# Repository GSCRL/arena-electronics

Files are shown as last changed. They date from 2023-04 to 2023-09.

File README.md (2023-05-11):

# arena-electronics

# Other Repos

UI / Webserver - https://github.com/fubarlabs/RobotCombatOverlay
ESP32 Firmware - https://github.com/GSCRL/bot-arena-control
## Build Arg Notes

```ini
check_skip_packages = yes
lib_deps = bblanchon/ArduinoJson
build_flags = -O2 -D DEBUG_ESP_PORT=Serial
build_unflags = -Os
```

# Broker Setup

```
allow_anonymous true

listener 1883
protocol mqtt

listener 9001
protocol websockets
```

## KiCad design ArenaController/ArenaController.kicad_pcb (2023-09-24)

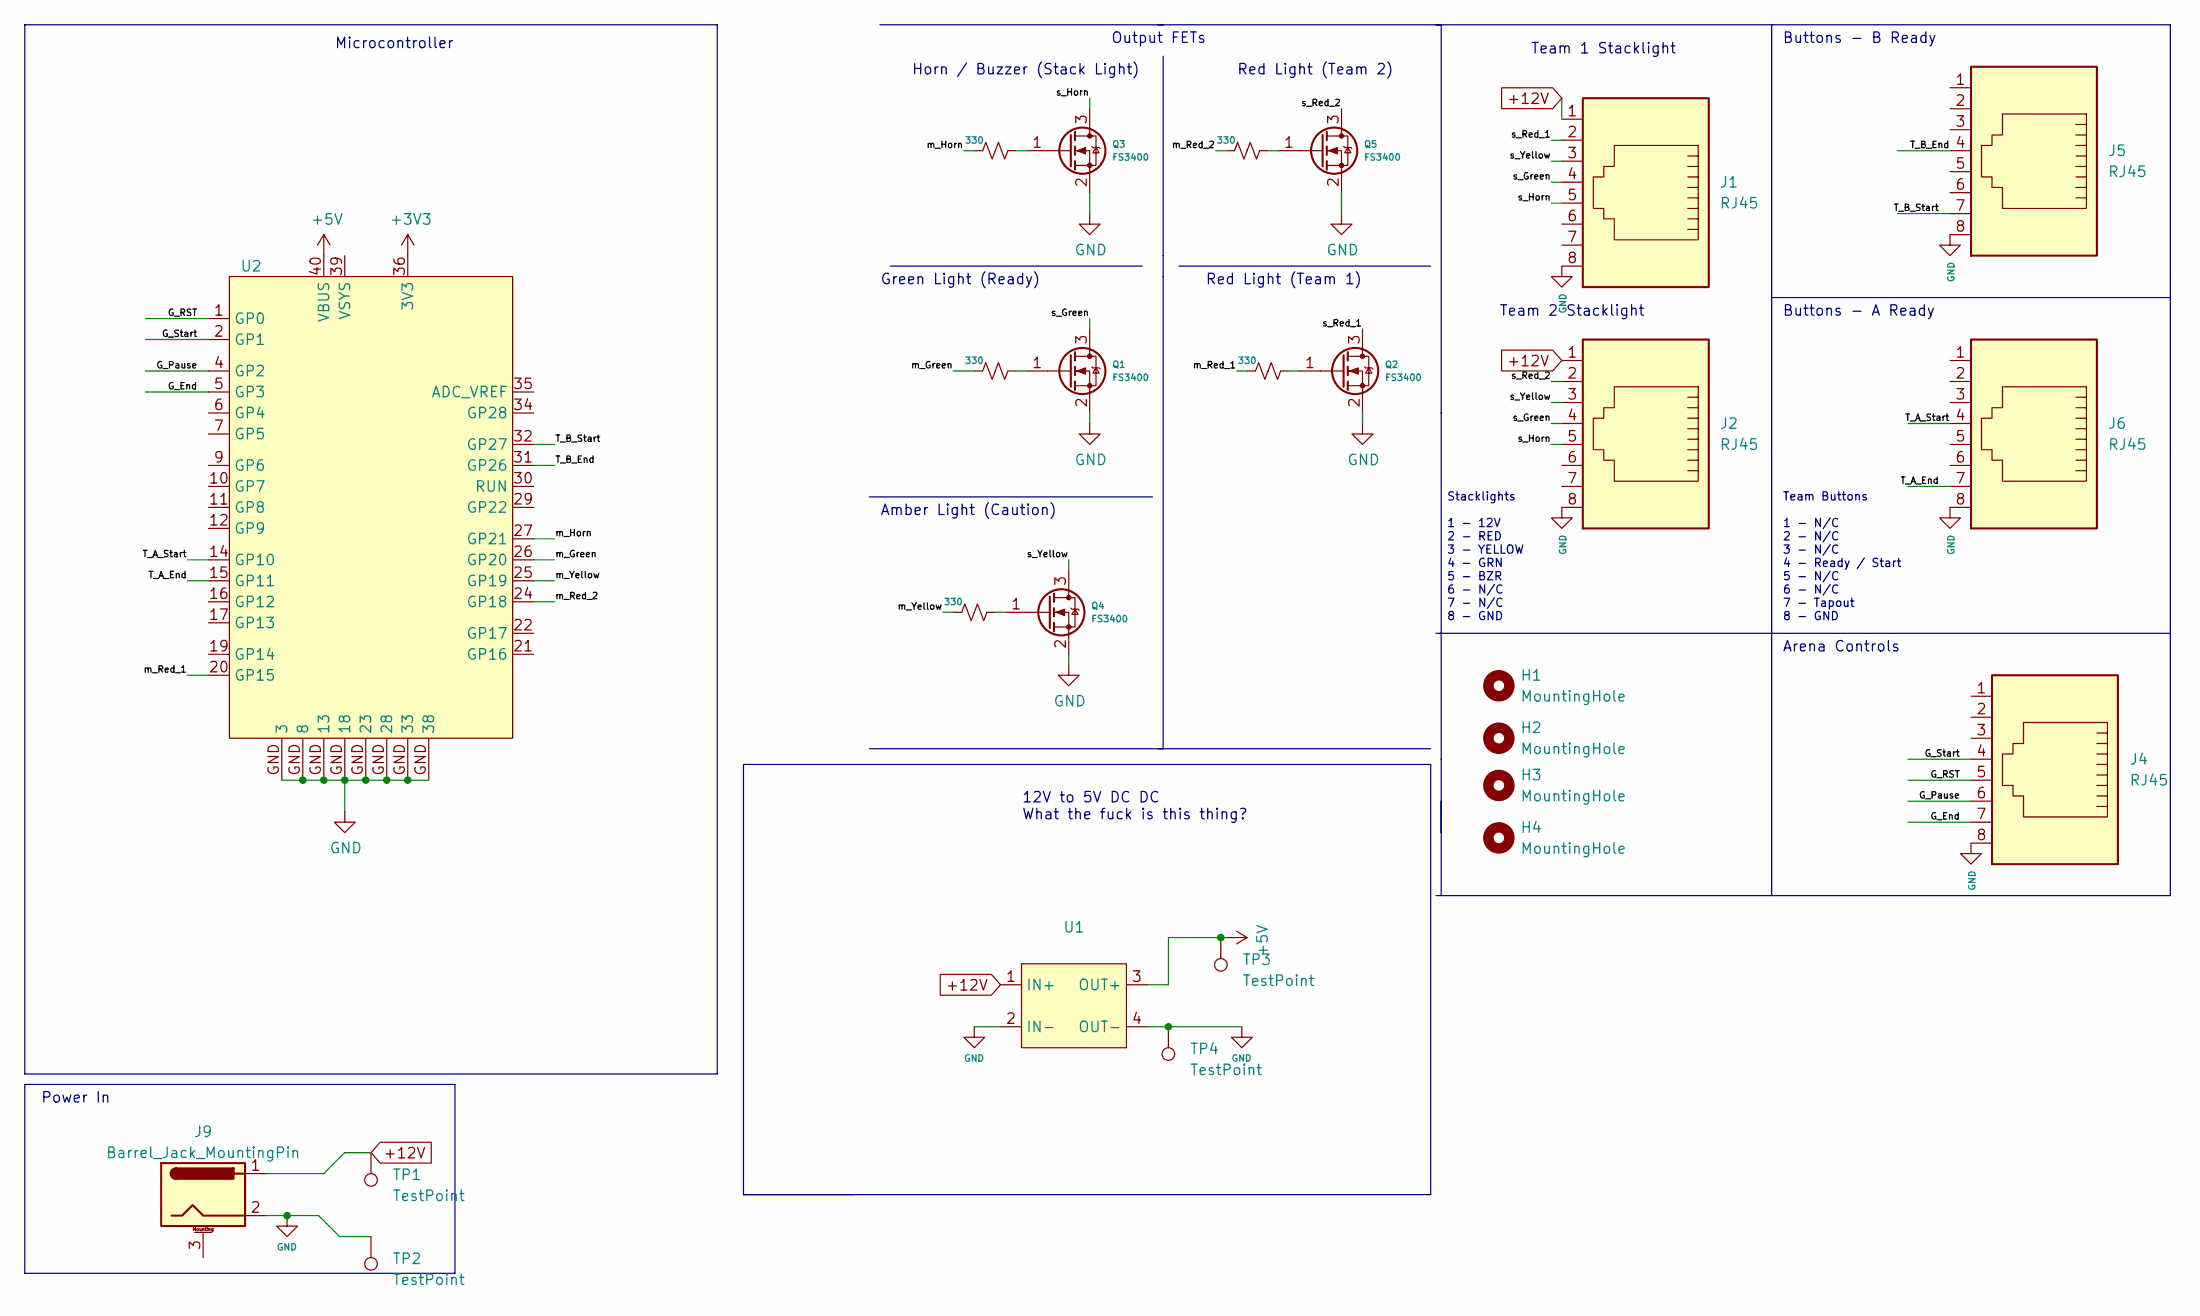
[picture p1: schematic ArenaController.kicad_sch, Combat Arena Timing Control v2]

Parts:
H1, H2, H3, H4: MountingHole; MountingHole_3.2mm_M3
J1, J2, J4, J5, J6: RJ45; RCH RC00139
J9: Barrel_Jack_MountingPin; BarrelJack_Horizontal
Q1, Q2, Q3, Q4, Q5: FS3400; SOT-23
R1, R2, R3, R4, R5: 330; R_1206_3216Metric_Pad1.30x1.75mm_HandSolder
TP1, TP2, TP3, TP4: TestPoint; TestPoint_Loop_D1.80mm_Drill1.0mm_Beaded
U1: LM2596_Module
U2: Raspberry_Pi_Pico_SMT_THT

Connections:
+3V3: U2.36 (3V3)
+5V: TP3.1, U1.3 (OUT+), U2.40 (VBUS)
+12V: J1.1, J2.1, J9.1, TP1.1, U1.1 (IN+)
/G_End: J4.7, U2.5 (GP3)
/G_Pause: J4.6, U2.4 (GP2)
/G_RST: J4.5, U2.1 (GP0)
/G_Start: J4.4, U2.2 (GP1)
/T_A_End: J6.7, U2.15 (GP11)
/T_A_Start: J6.4, U2.14 (GP10)
/T_B_End: J5.4, U2.31 (GP26)
/T_B_Start: J5.7, U2.32 (GP27)
/m_Green: R1.2, U2.26 (GP20)
/m_Horn: R2.2, U2.27 (GP21)
/m_Red_1: R5.2, U2.20 (GP15)
/m_Red_2: R4.2, U2.24 (GP18)
/m_Yellow: R3.2, U2.25 (GP19)
/s_Green: J1.4, J2.4, Q1.3 (D)
/s_Horn: J1.5, J2.5, Q3.3 (D)
/s_Red_1: J1.2, Q2.3 (D)
/s_Red_2: J2.2, Q5.3 (D)
/s_Yellow: J1.3, J2.3, Q4.3 (D)
GND: J1.8, J2.8, J4.8, J5.8, J6.8, J9.2, Q1.2 (S), Q2.2 (S), Q3.2 (S), Q4.2 (S), Q5.2 (S), TP2.1, TP4.1, U1.2 (IN-), U1.4 (OUT-), U2.GND (13)
unnamed: Q1.1 (G), R1.1
unnamed: Q2.1 (G), R5.1
unnamed: Q3.1 (G), R2.1
unnamed: Q4.1 (G), R3.1
unnamed: Q5.1 (G), R4.1

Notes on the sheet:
Amber Light (Caution)
Arena Controls
Microcontroller
Green Light (Ready)
Buttons - A Ready
Team 2 Stacklight
12V to 5V DC DC What the fuck is this thing?
Power In
Team 1 Stacklight
Output FETs
Horn / Buzzer (Stack Light)
Team Buttons 1 - N/C 2 - N/C 3 - N/C 4 - Ready / Start 5 - N/C 6 - N/C 7 - Tapout 8 - GND
Buttons - B Ready
Red Light (Team 1)
Red Light (Team 2)
Stacklights 1 - 12V 2 - RED 3 - YELLOW 4 - GRN 5 - BZR 6 - N/C 7 - N/C 8 - GND

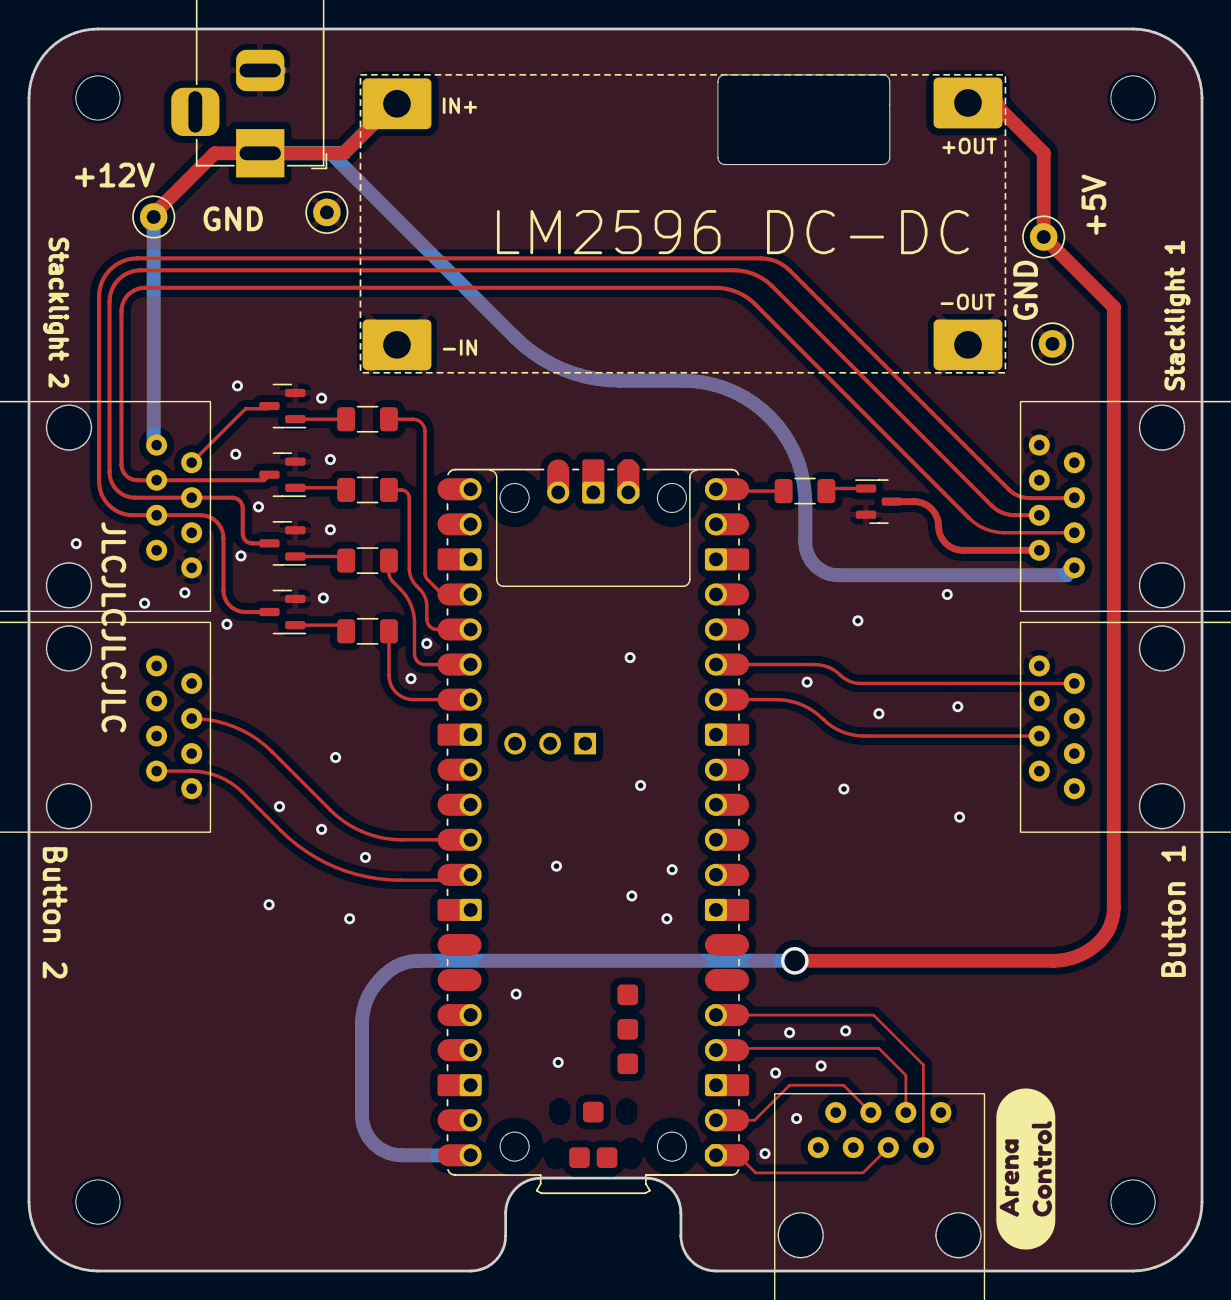
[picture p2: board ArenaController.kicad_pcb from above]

Board: 2 copper layers, 85.0 x 90.0 mm, 27 parts (0 on the bottom side), 26 nets.

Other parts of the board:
kibuzzard-638A219C: G***; kibuzzard-638A219C

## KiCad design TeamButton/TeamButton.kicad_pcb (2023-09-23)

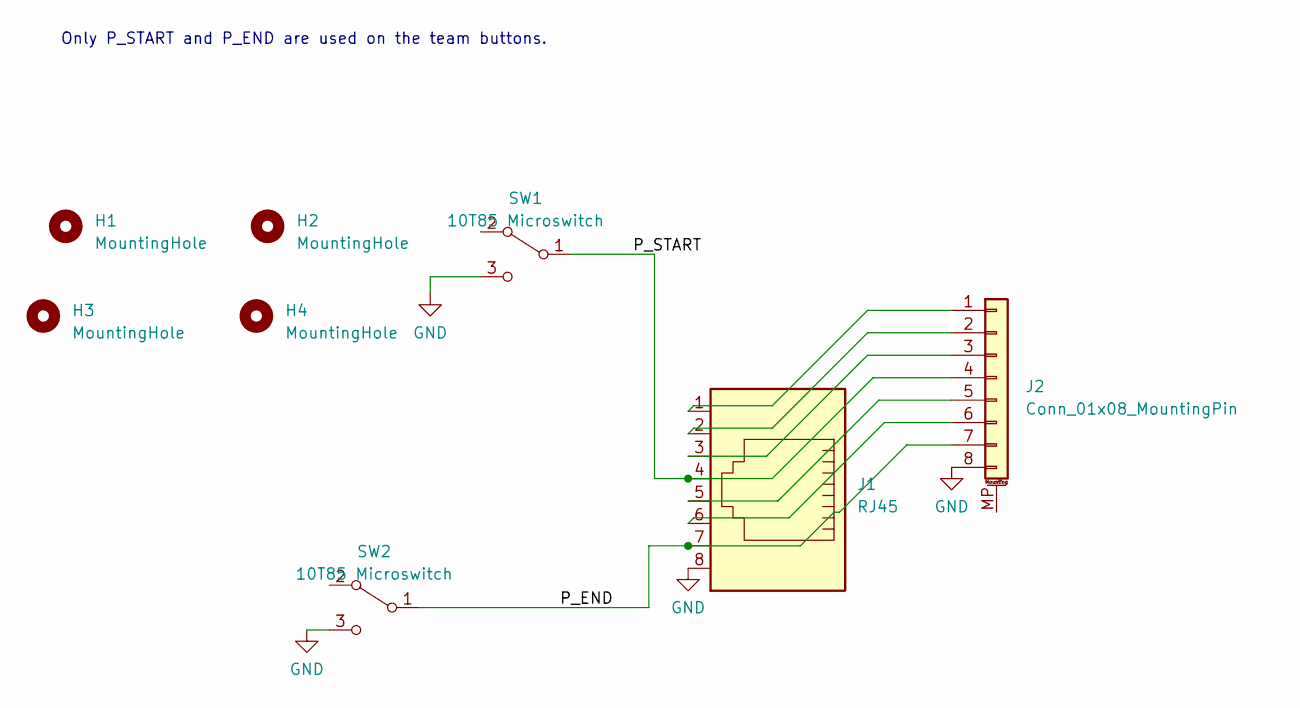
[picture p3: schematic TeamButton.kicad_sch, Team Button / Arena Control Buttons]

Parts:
H1, H2, H3, H4: MountingHole; MountingHole_3.2mm_M3
J1: RJ45; RCH RC00139
J2: Conn_01x08_MountingPin; PinSocket_1x08_P2.54mm_Horizontal
SW1, SW2: 10T85 Microswitch; 10T85 Microswitch with M3 mounts

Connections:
/P_END: J1.7, J2.7, SW2.1 (C)
/P_START: J1.4, J2.4, SW1.1 (C)
GND: J1.8, J2.8, SW1.3 (NO), SW2.3 (NO)
unnamed: J1.1, J2.1
unnamed: J1.2, J2.2
unnamed: J1.3, J2.3
unnamed: J1.5, J2.5
unnamed: J1.6, J2.6

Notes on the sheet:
Only P_START and P_END are used on the team buttons.

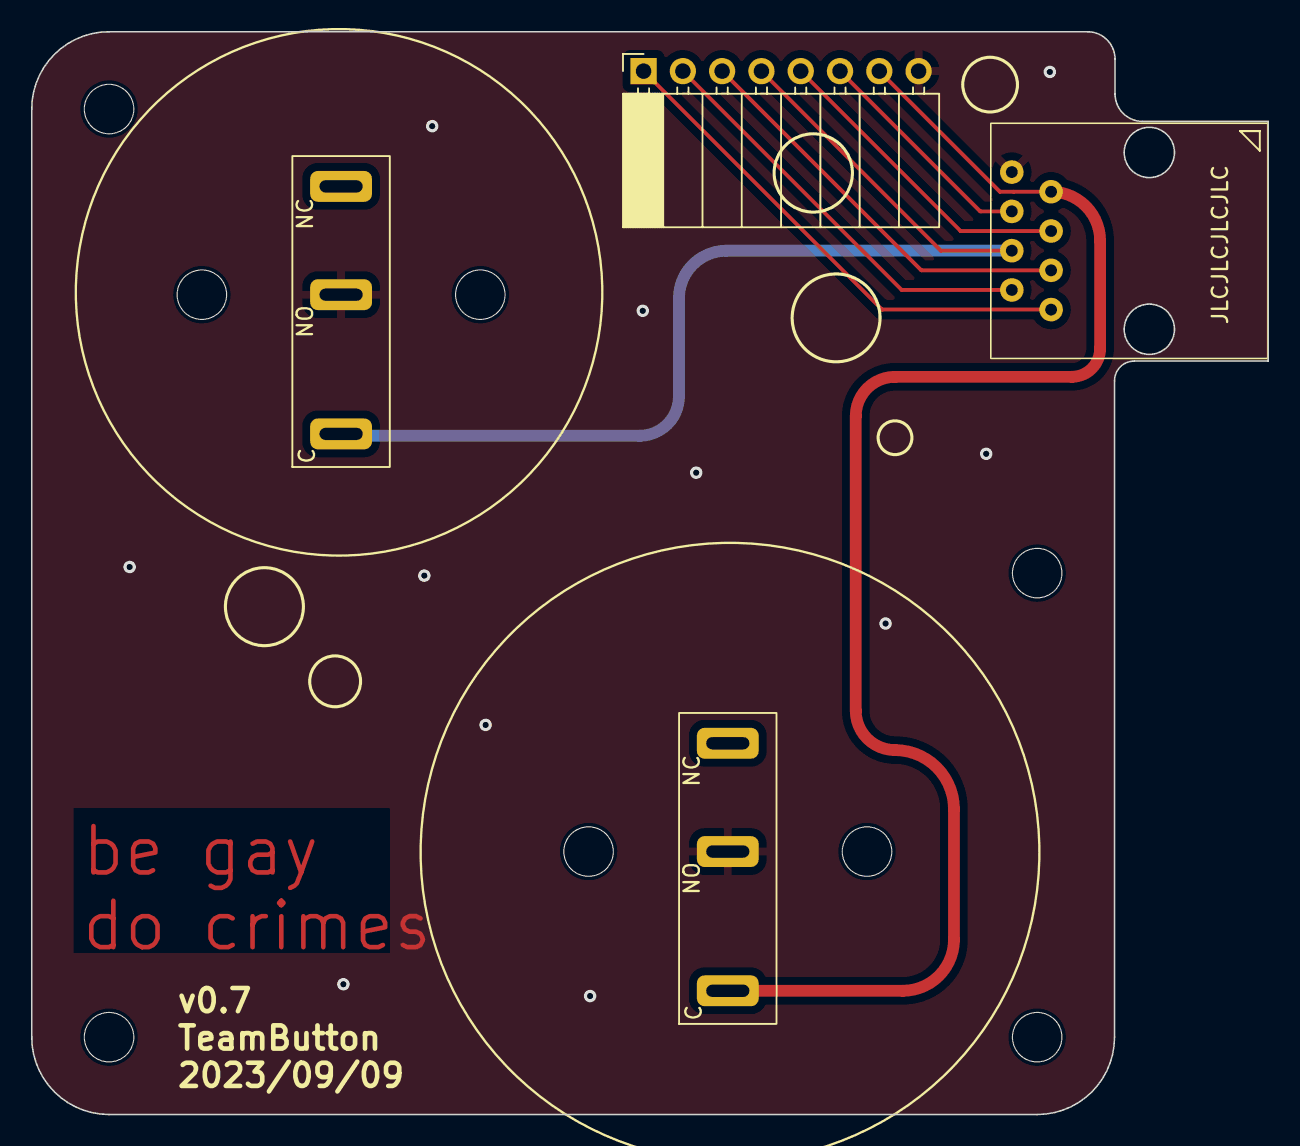
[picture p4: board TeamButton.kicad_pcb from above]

Board: 2 copper layers, 79.9 x 70.0 mm, 8 parts (0 on the bottom side), 8 nets.

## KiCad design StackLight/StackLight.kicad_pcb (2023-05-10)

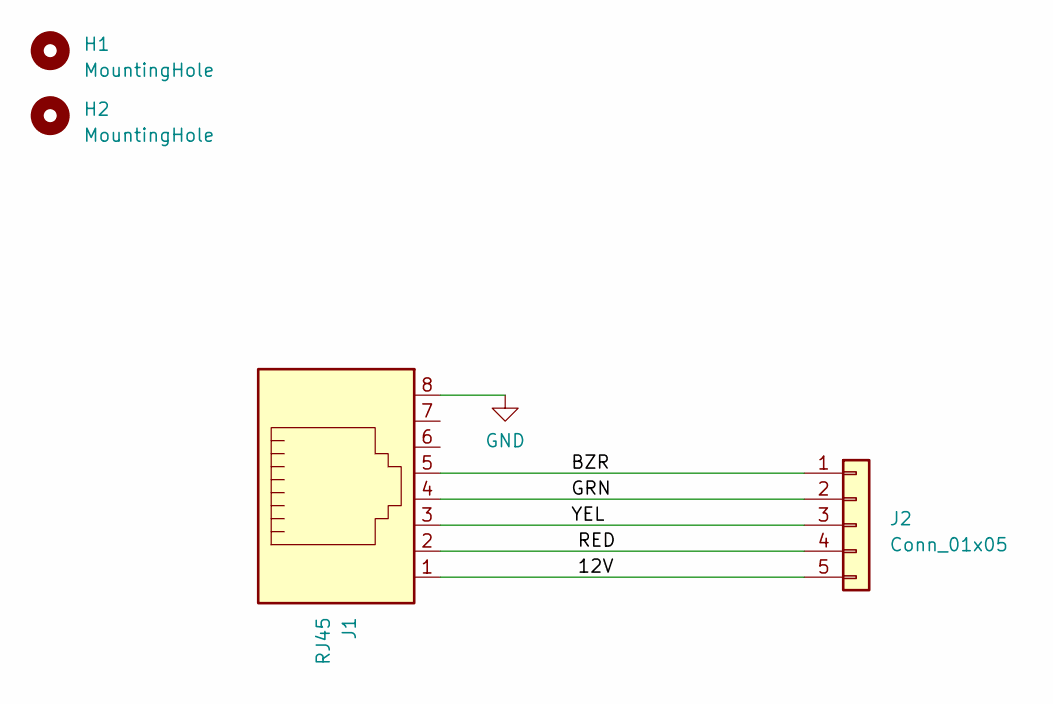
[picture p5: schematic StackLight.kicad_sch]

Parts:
H1, H2: MountingHole; MountingHole_3.2mm_M3
J1: RJ45; RCH RC00139
J2: Conn_01x05; SolderWire-1.5sqmm_1x05_P6mm_D1.7mm_OD3mm_Relief

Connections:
/12V: J1.1, J2.5
/BZR: J1.5, J2.1
/GRN: J1.4, J2.2
/RED: J1.2, J2.4
/YEL: J1.3, J2.3
GND: J1.8

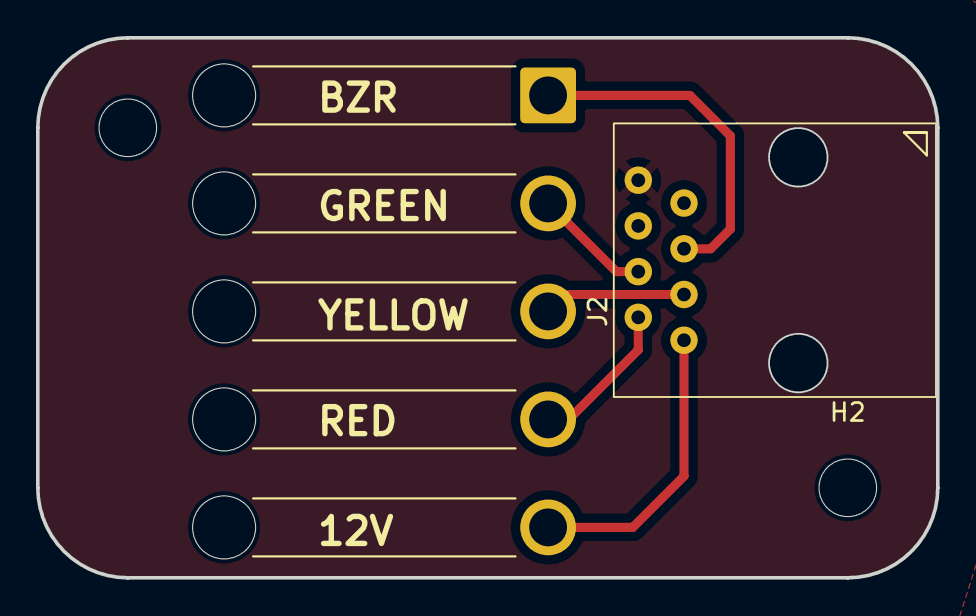
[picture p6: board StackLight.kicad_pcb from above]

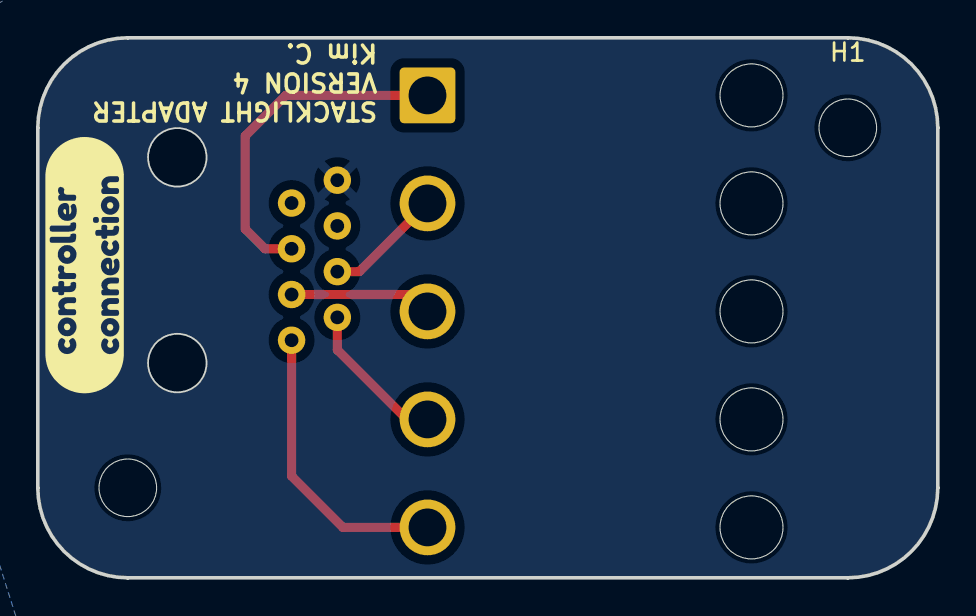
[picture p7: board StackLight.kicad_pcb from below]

Board: 2 copper layers, 50.0 x 30.0 mm, 5 parts (2 on the bottom side), 5 nets.

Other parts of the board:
kibuzzard-631545B4: G***; kibuzzard-631545B4

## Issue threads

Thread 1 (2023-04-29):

GPIO0 Use / Unable To Use Correct Pins

MC42, 2023-04-29:
Cannot use these pins for ESP32 DevkitC v4:

https://randomnerdtutorials.com/esp32-pinout-reference-gpios/

MC42, 2023-04-29:
Resolved in #decb0dff3449769d9eb318a582d3a359adc5a449

Closed 2023-04-29.

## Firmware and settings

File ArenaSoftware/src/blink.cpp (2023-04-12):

#include <Arduino.h>
#include <PushButton.h>

/*
** Robot Combat Arena Control Code
** Using Ardunio framework / ESP32 (maybe STM32 with GPIO changes)
** Read 8 buttons
** ready and tap out for 2 teams
** Match start / pause / end /reset for ref
** Serial out to hacked iCruze display boards
** Will control 1 or 2 "stoplight" towers with signal horns
** NF 2022/06/04

*/

// State diagram
/* no match states:
    Reset and ready for start ( solid yellow )
      team a ready
      team b ready
      both teams ready (blinking yellow)
    match pause (blinking yellow or blinking red / match timer paused)
    match tapout (blinking red)
    match end by KO (blinking red)
    match end by time (solid red)
  Match states
    Start pressed (3 secs of blinking yellow followed by green.  Match timer starts then)
    start pressed after pause (same as above with timer resuming)
    active match (solid green)
    10 sec count down (blinking green)
  Horn will sound at match end, time up or team tapout
*/
// inline echo for debug
#define DEBUG_ON 1
#define DEBUG_OFF 0
byte debugMode = DEBUG_ON;

#define DBG(...) debugMode == DEBUG_ON ? Serial.println(__VA_ARGS__) : NULL
#define DEBUG

// button GPIO's ESP32 / Change for STM32
#define TEAM_A_START 23
#define TEAM_A_END 22
#define TEAM_B_START 33
#define TEAM_B_END 32
#define MATCH_START 25
#define MATCH_PAUSE 26
#define MATCH_END 27
#define MATCH_RESET 14
// tower signal light GPIO's
#define R_LIGHT 2
#define Y_LIGHT 4
#define G_LIGHT 5
#define HORN 13

#define D_SER_TX 17
#define D_SER_RX 16

#define MATCH_LEN 180 // match len in sec ( 3 min)
#define MATCH_END_WARN 15 // ending warn time sec
#define BLINK_DELAY 500 // in ms
#define STARTUP_DELAY 3000 //3 sec
#define MAIN_LOOP_DELAY 5 // in ms
#define HORN_SHORT 1000 //ms
#define HORN_LONG 2000 //ms
#define DIS_DELAY 200 //ms display update rate

PushButton Start_A(TEAM_A_START);
PushButton End_A(TEAM_A_END);
PushButton Start_B(TEAM_B_START);
PushButton End_B(TEAM_B_END);
PushButton GameStart(MATCH_START);
PushButton GameOver(MATCH_END);
PushButton GamePause(MATCH_PAUSE);
PushButton GameReset(MATCH_RESET);

uint64_t Btn_timer;
uint64_t light_timer;
uint64_t Horn_timer;
uint64_t Timer_timer;
uint64_t Display_timer;
uint64_t Dis_min;
uint64_t Dis_sec;

// Match state
enum MatchState{ all_ready, team_a_ready, team_b_ready, starting, in_progress, ending, unpaused, paused, team_a_tap, team_b_tap, time_up, ko_end };
enum MatchState g_match;
bool g_Match_Reset;

uint64_t gMatchRunTime; //match run time ms
uint64_t gMatchStartTime; //match start time ms
uint64_t MatchSecRemain; // sec remaining
int64_t CountDownMSec; // count down
uint8_t isTimerRunning;
uint64_t gSDtimer; // used for start delay
uint64_t gBLtimer; // for light blinking
uint8_t gBLstate; // for light blinking
uint64_t gTootTimer; //for horn
uint8_t gHornState; // for horn
uint8_t gHornBlast;

// button reading and state setting is done here
void readBtns(MatchState &match, bool &Match_Reset)
{
  // note the button.cycleCount() resets the button press counter
  uint8_t BtnCycle;

  // if match is running these buttons are active
    if (match == MatchState::in_progress)
    {
      End_A.update();
      End_B.update();
      GameOver.update();
      GamePause.update();
      Match_Reset = false;
      DBG("test IP");
      // pause hit
      if (GamePause.isCycled())
      {
        BtnCycle = GamePause.cycleCount();
        match = MatchState::paused;
      }
      // team tap out
      if ((End_A.isCycled() || End_B.isCycled()) && (match == MatchState::in_progress))
      {
        // Team A has tapped out
        if(End_A.isCycled())
          match = MatchState::team_a_tap;
        // Team B has tapped out
        if(End_B.isCycled())
          match = MatchState::team_b_tap;
        BtnCycle = End_A.cycleCount();
        BtnCycle = End_B.cycleCount();
      }

      // Ref has ended the match
      if(GameOver.isCycled() && (match == MatchState::in_progress)) 
      {
        BtnCycle = GameOver.cycleCount();
        match = MatchState::ko_end;
      }
    }
    else
    // match is ended these are active
    // starting is the match start countdown state
    if ((match != MatchState::starting)||(match != MatchState::paused)||(match != MatchState::unpaused))
    {
      {
        GameStart.update();
        Start_A.update();
        Start_B.update();
        GameReset.update();
        //DBG("test Start");
        // this discards the reads on A, B and main start if not reset
        if (Match_Reset == false)
        {
          BtnCycle = Start_A.cycleCount();
          BtnCycle = Start_B.cycleCount();
          BtnCycle = GameStart.cycleCount();
        }
        if (GameReset.isCycled())
        {
          Match_Reset = true;
          BtnCycle =GameReset.cycleCount();
        }

        // check to see if both teams are ready
        if (Start_A.isCycled() and Start_B.isCycled())
        {
          match = MatchState::all_ready;
          BtnCycle = Start_A.cycleCount();
          BtnCycle = Start_B.cycleCount();
        }
        else
        {
          if (Start_A.isCycled())
          {
            match = MatchState::team_a_ready;
          }
          if (Start_B.isCycled())
          {
            match = MatchState::team_b_ready;
          }
        }
        // if everyone is ready and start is pressed
        if (GameStart.isCycled() and (match == MatchState::all_ready))
        {
          BtnCycle = GameStart.cycleCount();
          BtnCycle = GameReset.cycleCount();
          match = MatchState::starting;
        }
      }
    }
    // match paused
    else
    {
      if(match == MatchState::paused)
      {
        GameStart.update();
        if(GameStart.isCycled())
        {
          match = unpaused;
          BtnCycle = GameStart.cycleCount();
        }
      }
    }

}

// used to blink the light tower
void blink(u_int8_t &state, uint64_t &lastBlink, u_int8_t ledGPIO)
{
  if((millis() - lastBlink) > BLINK_DELAY)
  {
    if (state > 0)
    {
      digitalWrite(ledGPIO, HIGH);
      state = 0;
    }
    else
    {
      digitalWrite(ledGPIO, LOW);
      state = 1;
    }
    lastBlink = millis();
  }
}

// handle lights here
void setLights(MatchState &match, u_int8_t Match_Reset, u_int64_t &SDtimer)
{
  
// all lights off
  if((Match_Reset) && (match != MatchState::starting))
  {
    digitalWrite(G_LIGHT,LOW);
    digitalWrite(Y_LIGHT,LOW);
    digitalWrite(R_LIGHT,LOW);
  }
  // match in progress
  if (match == in_progress)
  {
    digitalWrite(G_LIGHT,HIGH);
    digitalWrite(Y_LIGHT,LOW);
    digitalWrite(R_LIGHT,LOW);
  }
  // match is stopped
  // if ((g_match != in_progress) || (g_match != starting) || (g_match != paused) || (g_match != unpaused))
  // not sure if enum can be used this way
  if ((match < 3) && (match > 6))
  {
    digitalWrite(G_LIGHT,LOW);
    //digitalWrite(Y_LIGHT,LOW);
    digitalWrite(R_LIGHT,HIGH);
  }
  // match is starting
  // blink yellow for 3 sec, red out, green out
  if(match == MatchState::starting)
  {
    if((millis()-SDtimer) < STARTUP_DELAY)
      blink(gBLstate, gBLtimer, Y_LIGHT);
    else
      match=MatchState::in_progress;
    SDtimer = millis();
  }
  // match is paused
  // red is lit yellow is blinking
  if(match == MatchState::paused)
  {
    blink(gBLstate, gBLtimer, Y_LIGHT);
    digitalWrite(R_LIGHT,HIGH);
  }
  // match is ending (within 15 sec of end)
  // blink green
  if(match == MatchState::ending)
  {
    blink(gBLstate, gBLtimer, G_LIGHT);
  }

  // to do when everything working
  // Team A tap blink A tower red
  // Team B tap blink B tower red
  // for now just blink both towers red
}

// light debug function
void LightDebugPrint(MatchState &match, u_int8_t Match_Reset, u_int64_t &SDtimer)
{
  switch (match)
  {
  case MatchState::all_ready:
    Serial.println("All ready");
    break;
  case MatchState::team_a_ready:
    Serial.println("team_a_ready");
    break;
  case MatchState::team_b_ready:
    Serial.println("team_b_ready");
    break;
  case MatchState::starting:
    Serial.println("starting");
    break;
  case MatchState::in_progress:
    Serial.println("in_progress");
    break;
  case MatchState::ending:
    Serial.println("ending");
    break;
  case MatchState::unpaused:
    Serial.println("unpaused");
    break;
  case MatchState::paused:
    Serial.println("paused");
    break;
  case MatchState::team_a_tap:
    Serial.println("team_a_tap");
    break;
  case MatchState::team_b_tap:
    Serial.println("team_b_tap");
    break;
  /*case MatchState::time_up:
    Serial.println("time_up");
    break;
  case MatchState::ko_end:
    Serial.println("ko_end");*/
  default:
    break;
  }
  if(match == MatchState::starting)
  {
    if((millis()-SDtimer) < STARTUP_DELAY)
      blink(gBLstate, gBLtimer, Y_LIGHT);
    else
      match=MatchState::in_progress;
    SDtimer = millis();
  }
}

// used to sound horn (yet another timer)
void soundHorn(u_int8_t &hornBlast, uint64_t &hornTime, u_int32_t tootLen, u_int8_t GPIO)
{
  u_int8_t state  = hornBlast % 2;
  if((millis() - hornTime) > tootLen)
  {
    if (state > 0)
    {
      digitalWrite(GPIO, HIGH);
    }
    else
    {
      digitalWrite(GPIO, LOW);
    }
    hornTime = millis();
    hornBlast++;
  }
}
// update and display match time
void match_timer(u_int64_t StartTime, u_int64_t &timerValue, u_int8_t &running)
{
  if ((running) && (timerValue < MATCH_LEN * 1000))
    timerValue = millis() - StartTime;
  else
    running = false;
}

void setup() {
  Serial.begin(115200);
  Serial1.begin(9600,SERIAL_8N1,D_SER_RX,D_SER_TX);
  pinMode(R_LIGHT,OUTPUT);
  pinMode (Y_LIGHT,OUTPUT);
  pinMode (G_LIGHT, OUTPUT);
  // check lights
  digitalWrite(G_LIGHT,HIGH);
  digitalWrite(Y_LIGHT,HIGH);
  digitalWrite(R_LIGHT,HIGH);
  Serial.println("test");
  delay(1000);
  digitalWrite(G_LIGHT,LOW);
  digitalWrite(Y_LIGHT,LOW);
  digitalWrite(R_LIGHT,LOW);
  // check horn
  digitalWrite(HORN,HIGH);
  delay(200);
  digitalWrite(HORN,LOW);
  g_Match_Reset = false;
  isTimerRunning = false;
  gMatchRunTime = 0;
  gMatchStartTime = 0;
  gSDtimer = 0;
  CountDownMSec = 0;
  gBLtimer = millis();
  Btn_timer = millis();
  g_match = MatchState::time_up;
  Serial1.println("---Display Test----");
  Serial1.println("---Line 2----");
}

void loop() 
{
  
  // Button reading is here
  if ((millis()-Btn_timer) > MAIN_LOOP_DELAY)
  {
    readBtns(g_match, g_Match_Reset);
    DEBUG("test prime");
    // set startup delay - match will be inprogress after this is done
    if ((g_match == MatchState::starting)&&(gSDtimer == 0))
      gSDtimer = millis();
    else if (g_match == MatchState::starting)
    {
      CountDownMSec = STARTUP_DELAY -(millis() - gSDtimer);
      if (CountDownMSec < 5)
      {
        // start match reset count down timer
        g_match = MatchState::in_progress;
        CountDownMSec = 0;
        gSDtimer = 0;
      }
    }
    Btn_timer = millis();
  }
  // handle lights
  #ifdef DEBUG
  if ((millis()-light_timer) > MAIN_LOOP_DELAY + 200)
  {
    LightDebugPrint(g_match, g_Match_Reset, gSDtimer);
    light_timer = millis();
  }
  #else
  if ((millis()-light_timer) > MAIN_LOOP_DELAY + 1)
  {
    setLights(g_match, g_Match_Reset, gSDtimer);
    light_timer = millis();
  }
  #endif
  // handle horn
  #ifdef DEBUG
  #else
  if ((millis()- Horn_timer) > MAIN_LOOP_DELAY * 2 )
  {
      // short horn on start or pause
      /*
      if(g_match == MatchState::starting)
      {
        while (gHornBlast < 6)
        {
          soundHorn(gHornBlast,gTootTimer,HORN_SHORT,HORN);
        }
      }
      else
        if(g_match < 8)
          gHornBlast = 0;
      // long horn on match end
      if(g_match > 7)
      {
        while (gHornBlast < 2)
        {
          soundHorn(gHornBlast,gTootTimer,HORN_LONG,HORN);
        }
      }
      else
        if(g_match!=MatchState::starting)
          gHornBlast = 0;
      */
      Horn_timer = millis();
  }
  #endif

  // update match timer
  if ((millis() + Timer_timer) > MAIN_LOOP_DELAY)
  {
    //start timer
    if((g_match == MatchState::in_progress)&&(isTimerRunning == false))
    {
      gMatchStartTime = millis();
      isTimerRunning = true;
    }
    //restart after pause
    if((g_match == MatchState::unpaused)&&(isTimerRunning == false))
    {
      isTimerRunning = true;
      g_match = MatchState::in_progress;
    }
    //stop timer
    if(g_match != MatchState::in_progress)
      isTimerRunning = false;

    //update timer
    if(((g_match == MatchState::in_progress)||(g_match == MatchState::ending))&&(isTimerRunning == true))
    {
      match_timer(gMatchStartTime, gMatchRunTime, isTimerRunning);
      if(isTimerRunning == false)
        g_match = MatchState::time_up;
    }
    // check for match ending
    MatchSecRemain = MATCH_LEN - ((gMatchRunTime - gMatchStartTime)/1000);
    if (MatchSecRemain < MATCH_END_WARN)
      g_match  = MatchState::ending;
    Timer_timer = millis();
  }

  // update char display
  // will send info out via serial
  if ((millis()-Display_timer) > DIS_DELAY)
  {
    // using the 2 x 20 line iCruze display
    // refresh display every 200 ms 
    // display time remaining in min : sec on first line
    // status display on second
    Dis_min = MatchSecRemain / 60;
    Dis_sec = MatchSecRemain % 60;
    if(g_match == MatchState::in_progress)
    {
      Serial1.print(Dis_min);
      Serial1.print(":");
      Serial1.printf("%02d",Dis_sec);
      Serial1.println(" Remaining");
      Serial1.println("Match in Progress");
    }
    if(g_match == MatchState::paused)
    {
      Serial1.print(Dis_min);
      Serial1.print(":");
      Serial1.printf("%02d",Dis_sec);
      Serial1.println(" Remaining");
      Serial1.println("--Paused --");
    }
    if(g_match == MatchState::starting)
    {
      Serial1.print("Starting in: ");
      Serial1.printf("%02d",(gSDtimer/1000));
      Serial1.println();
      Serial1.println("ALL READY-Starting");
    }
    if(g_match == MatchState::time_up)
    {
      Serial1.println("--- Time's Up ---");
      Serial1.println("-- MATCH OVER ---");
    }
    if(g_match == MatchState::team_a_tap)
    {
      Serial1.print(Dis_min);
      Serial1.print(":");
      Serial1.printf("%02d",Dis_sec);
      Serial1.println(" -MATCH OVER-");
      Serial1.println("--TEAM A TAPOUT--");
    }
    if(g_match == MatchState::team_b_tap)
    {
      Serial1.print(Dis_min);
      Serial1.print(":");
      Serial1.printf("%02d",Dis_sec);
      Serial1.println(" -MATCH OVER-");
      Serial1.println("--TEAM B TAPOUT--");
    }
    if(g_match == MatchState::ko_end)
    {
      Serial1.print(Dis_min);
      Serial1.print(":");
      Serial1.printf("%02d",Dis_sec);
      Serial1.println(" -MATCH OVER-");
      Serial1.println("-- BY KNOCKOUT --");
    }
    if(g_match == MatchState::all_ready)
    {
      Serial1.println("-- 3 min clock ---");
      Serial1.println("--- ALL READY ---");
    }
    if((g_match != MatchState::all_ready)&&(g_Match_Reset == true)&&(g_match != MatchState::starting))
    {
      Serial1.println("-- WAITING FOR ---");
      Serial1.println("----- READY -----");
    }
    Display_timer = millis();
  }
}

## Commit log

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2022-12-24 Add the funky stuff to start. This will be hell btw.
    [LightController.kicad_sch]
2022-12-24 Updated first half of schematic, mostlyish. Lots to go for lighting.
    [LightController.kicad_sch]
2022-12-25 Update roughly, using the same schematic for the 3v3 and 5v stuff, still need to figure out values, etc.
    [LightController.kicad_pcb, LightController.kicad_sch]
2022-12-30 Add footprints and shit.
    [LightController.kicad_pcb, LightController.kicad_sch]
2023-01-26 Bring in old schematic for cleanup / base work.
    [ArenaController.kicad_pcb, ArenaController.kicad_sch, ArenaController.sch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]
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2023-02-17 Add microswitch for start buttons.
    [ArenaController.kicad_pcb, ArenaController.kicad_sch]
2023-03-19 Added new files, swap to new FET for toggling, added FET as symbols.
    [ArenaController.kicad_pcb, ArenaController.kicad_sch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]
2023-03-22 Added new DC DC symbol.
    [ArenaController.kicad_pcb, ArenaController.kicad_sch]
2023-03-22 Added more SMD nightmare parts.
    [ArenaController.kicad_pcb, ArenaController.kicad_sch]
2023-03-22 Swapped to ESP32 Devkit 4.
    [ArenaController.kicad_pcb, ArenaController.kicad_sch]
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2023-03-27 small boardwork cleanup to try and lay it out.
    [ArenaController.kicad_pcb, ArenaController.kicad_sch]
2023-03-28 Started to organize board proper, did filled areas for 12V->5V input section.
    [ArenaController.kicad_pcb]
2023-03-29 Updated layout, added major routing. Still need connector for the WS2812B output and pin relayout.
    [ArenaController.kicad_pcb, ArenaController.kicad_sch]
2023-03-30 Tiny cleanup, workable version, yay.
    [ArenaController.kicad_pcb]
2023-03-31 Revision .4 layout with a sane ground plane, do fix the footprint shit tho
    [ArenaController.kicad_pcb, ArenaController.kicad_sch]
2023-04-05 Release v.4 for April event.
    [ArenaController-B_Cu.gbr, ArenaController-B_Mask.gbr, ArenaController-B_Paste.gbr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]
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2023-04-13 Updated team buttonboard to use M3 fasteners!
    [TeamButton.kicad_pcb, TeamButton.kicad_sch]
2023-04-14 Work day fixes for schematic, including re-polarizing the caps.
    [ArenaController.kicad_pcb, ArenaController.kicad_sch]
2023-04-14 Updated Button and Stacklight PCB to not have backwards fucking footprint shit.
    [StackLight.kicad_pcb, StackLight.kicad_sch, TeamButton.kicad_pcb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]
2023-04-14 Added SPIFFS note for if we need to use embedded FS stuff. Yay!
    [ArenaController.kicad_sch]
2023-04-14 Update to non-hole design. Verify wire gagues.
    [StackLight.kicad_pcb, StackLight.kicad_sch]
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2023-04-14 Added spacer mounting holes to board in case are needed. Insert through back first. Use smaller fasteners, etc. Only one hole should be needed.
    [TeamButton.kicad_pcb, TeamButton.kicad_sch]
2023-04-14 Added visual flourish and confirmed microswitch locations.
    [TeamButton.kicad_pcb]
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2023-04-14 Added wire strain relief that should fit.
    [StackLight.kicad_pcb, StackLight.kicad_sch]
2023-04-29 Update PCB errors and also remove software from this repo.
    [ArenaController-B_Cu.gbr, ArenaController-B_Mask.gbr, ArenaController-B_Paste.gbr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]
2023-04-29 Swap to a footprint with the correctly named pin in our project repo. Yay!
    [ArenaController.kicad_pcb, ArenaController.kicad_sch]
2023-05-04 Added initial teamsign and update symbol mistakes, mostly.
    [ArenaController.kicad_pcb, ArenaController.kicad_sch]
2023-05-04 Add team sign to gitignore and actually add stuff. Yay!
    [TeamSign.kicad_pcb, TeamSign.kicad_sch]
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2023-05-04 Update fp to include fixed keepouts for the THT part module.
    [ArenaController.kicad_pcb, ArenaController.kicad_sch]
2023-05-05 Initial footprint drag-in, add the svg, make the project libraries, and other stuff. Yay!
    [TeamSign.kicad_sch, three_digit.kicad_pcb]
2023-05-05 Add SK6812-Side-A footprint/symbol to working area, as well as swapped to a stacklight connection that has a ground pin at the end for generic 12v power use. yay!
    [ArenaController.kicad_pcb, ArenaController.kicad_sch, TeamSign.kicad_pcb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]
2023-05-06 Added subsheet for the other LEDs, still need to fix the capacitor footprint, but making solid progress it seems? Wild!
    [LED_Array_1.kicad_sch, TeamSign.kicad_pcb, TeamSign.kicad_sch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]
2023-05-06 Add PEM nut footprint starter to library, also did small tweaks to BOM and updated symbols to include the barrel jack antics. Yay!
    [LED_Array_1.kicad_sch, TeamSign.kicad_pcb, TeamSign.kicad_sch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]
2023-05-06 Shrink the labels for the side-firing SK6812SideAs, as well as start the footprint of the SMTSOM2.550BTR PEM nut.
    [TeamSign.kicad_pcb]
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2023-05-07 Added gerbers for TS to the ignore, plus added level shifting. Yay!
    [TeamSign.kicad_pcb, TeamSign.kicad_sch]
2023-05-07 Resolve subsheet antics... Yay.
    [LED_Array_1.kicad_sch, TeamSign.kicad_pcb, TeamSign.kicad_sch]
2023-05-07 Placed so many capacitors, dear lord
    [TeamSign.kicad_pcb]
2023-05-10 Added reset pins back in and broke out the pins in the team control area; should be easier now. Yay!
    [ArenaController.kicad_pcb, ArenaController.kicad_sch, TeamButton.kicad_pcb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]
2023-05-10 Updated PCB revisions, swapped to larger footprint for stacklight connector, release cutting soon.
    [ArenaController-B_Cu.gbr, ArenaController-B_Mask.gbr, ArenaController-B_Paste.gbr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]
2023-05-10 Update repo to use consistent gerber outputs; yay!
    [AudioController.kicad_pcb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]
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2023-05-10 Added power area, and started drawing pours.
    [TeamSign.kicad_pcb, TeamSign.kicad_sch]
2023-05-10 Fight with Freerouting, turns out there's a bug. Routing by hand.
    [TeamSign.kicad_pcb]
2023-05-10 Mostly routed, needs side-firing cleanup.
    [TeamSign.kicad_pcb]
2023-05-10 Changed thermal relief style, updated LEDs, seem to have worked? idk, yay
    [LED_Array_1.kicad_sch, TeamSign.kicad_pcb, TeamSign.kicad_sch]
2023-05-11 Move connectors to front of board so they're in the bulky area.
    [TeamSign.kicad_pcb, TeamSign.kicad_sch]
2023-05-11 Updated link, BOM, and some general sanity changes.
    [TeamSign.kicad_sch, rough_bom.ods]
2023-05-12 Tiny PCB trace edits.
    [TeamSign.kicad_pcb]
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2023-05-22 Update BOM + team sign PCB to not have diffuser issue.
    [TeamSign.kicad_pcb, rough_bom.ods]
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2023-06-06 Update ArenaController footprints to be over the edge and line up with the printed enclosure.
    [ArenaController-B_Cu.gbr, ArenaController-B_Mask.gbr, ArenaController-B_Paste.gbr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]
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2023-06-09 Update board to have less skullfscked routing and removed unused projects.
    [ArenaController.kicad_pcb, ArenaController.kicad_sch, AudioController.kicad_pcb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]
2023-06-19 Added test points and 3D model for pin headers to the ESP32 footprint.
    [ArenaController.kicad_pcb, ArenaController.kicad_sch]
2023-06-19 move power jack further right to permit complete enclosure for sealing sanity.
    [ArenaController.kicad_pcb]
2023-06-24 Updated arena controls, delete team signs that are now deprecated, added more footprints.
    [ArenaController.kicad_pcb, ArenaController.kicad_sch, LED_Array_1.kicad_sch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]
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2023-08-26 Changed output tool to fix missing drill files, at least in theory.
    [ArenaController-B_Cu.gbr, ArenaController-B_Mask.gbr, ArenaController-B_Paste.gbr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]
2023-08-27 Update footprint library and also project to KiCAD 7.99 Nightly due to the properties pane making fixing the RP2040W footprint SO MUCH easier. Still verify, etc.
    [ArenaController.kicad_pcb]
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2023-09-23 Fix footprint issue with the LM2596 and re-spin for next use.
    [ArenaController-B_Cu.gbr, ArenaController-B_Mask.gbr, ArenaController-B_Paste.gbr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]
2023-09-24 Update LM2596 to add THT cutout for potentiometer for adjustment, yay
    [ArenaController.kicad_pcb]
2023-09-24 Tiny footprint keepout to hide THT pot adjustment for real this time.
    [ArenaController.kicad_pcb]
